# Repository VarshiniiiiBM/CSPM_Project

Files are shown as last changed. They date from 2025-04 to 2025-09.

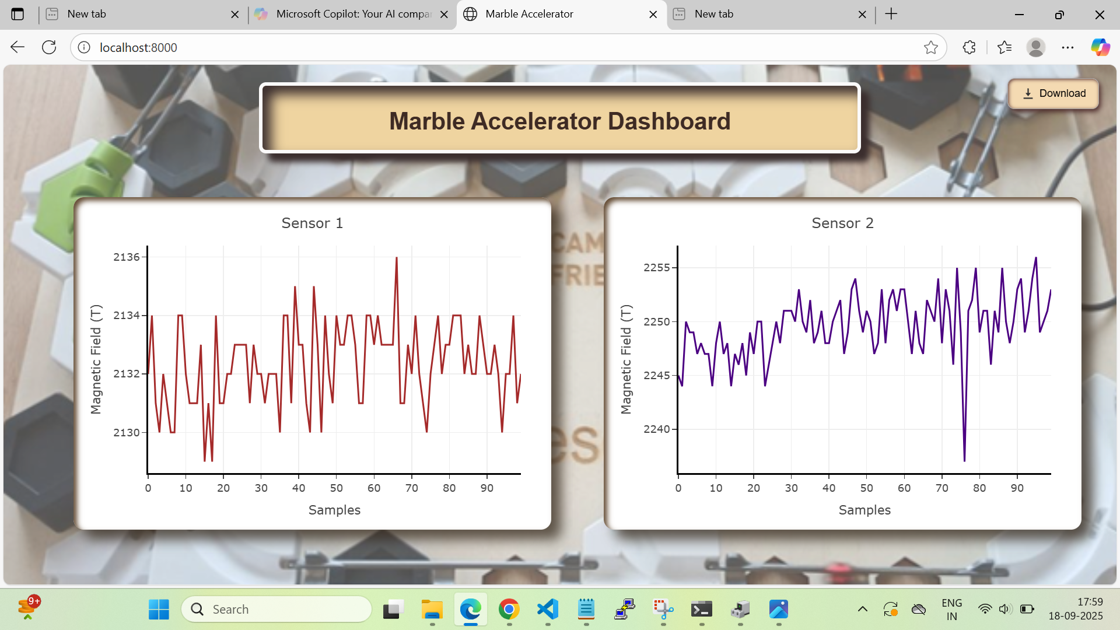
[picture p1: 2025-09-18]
Data_visualization/Fastapi_webserver/Result_img/img_3.png

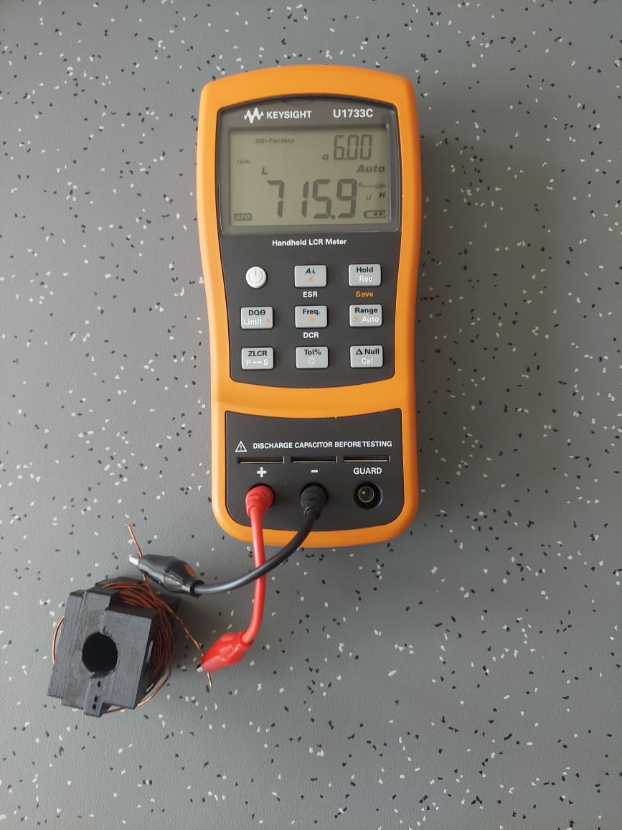
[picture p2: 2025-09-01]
Induction measurement/Coil 2 Inductance.jpeg

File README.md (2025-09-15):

# CSPM_Project
Marble Accelerator

## Team 

Members:

- Varshini Barallu Manjunath
- Rohith Joy
- Murtuza Udaipurvala
- Abdul Manaf 
- Anisha Bhanderi
- Smit Patel Kumar
- Fabian Mink (Supervisor)

## Links

Hessenbox: https:https://next.hessenbox.de/index.php/s/KFFSPPiGzwdTdbN

## Rules for writing equations, physical units and quantities

When formulating expressions, the internationally recognized rules of the SI system must be strictly adhered to. This applies to both presentation slides and reports. Failure to comply with these rules will result in a significant reduction in the grade for the formal criteria of the project work.

The SI-Brochure provides a good overview:

https://www.bipm.org/en/publications/si-brochure

A checklist can be found at the beginning of this document, pages v - vi:

https://physics.nist.gov/cuu/pdf/sp811.pdf

## Components

List of items borrowed from Fabian to be returned at the end of the project:

- Gravitrax Components (Box, Baseplate, 2x Curves, curved tunnel, 2x rails, sample coil designs)
- BTS7960 H-Bridge Board
- KY-035 Hall Sensors
- 2x Board STM32L476 Nucleo, 1x USB Cable
- Capacitor 22mF, 50V and Capacitor bank 20x1.5mF, 25V (2025-06-12)
- Lab Power Supply PeakTech 6226 (2025-07-01)
- Oscilloscope TDS 1012 + 2 Probes + USB CF Card Reader + Transport Bag (2025-09-15)

The project grades will only be entered into the examination system when all parts have been returned in good condition!

## Presentation And Report 
- Report Submission Date : 19th Semptember
- Presentation Submission Date : 21st Semptember
- Presentation Data : 23rd Semptember 
- Presentation Format: Total 20 min, including 5 mins for project video.

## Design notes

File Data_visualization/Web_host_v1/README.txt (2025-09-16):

# STM32 Real-Time Data Visualization
 
This Python script enables real-time data visualization of sensor data from an STM32 through serial communication. The data can be visualized both on a desktop application (PyQt6) and on a web interface (Plotly.js), accessible remotely through FastAPI, WebSockets, and ngrok. A QR code is generated at runtime, allowing instant access to the live charts on mobile devices.

## Features

* **Real-time Data Streaming**: JSON chunks sent every 10 ms, each containing 100 samples of D1–D3.
* **Derived Parameter (D4)**:Is computed from (D1)[asumed as Kinetic Energy].

* **Desktop Visualization**:

  * PyQt6 window opens automatically on script execution.
  * Charts for D1, D2, D3, and D4 with automatic Y-axis scaling.
  *An update from  Matplotlib has been applied for smooth rendering and lag-free visualization.

* **Web Visualization**:

  * FastAPI + WebSockets for real-time data broadcast.
  * Ngrok tunneling removes dependency on the same local network.
  * Multiple devices can be connected simultaneously by scanning the QR code generated.
  * QR code generation for quick mobile access.
  * Charts can be downloaded directly on mobile or PC.
  * Accessible on PC locally where script is run, on browser at `https://<PC-IP>:8000`.

* **Reset Functionality**: Data clears automatically when STM32 reset button is pressed.

---

## Data Format

Example JSON chunk received from STM32:

```json
{
  "D1": [1.61, 1.61, 1.61, ...],
  "D2": [84639, 84640, 84641, ...],
  "D3": [-200, 200, -200, ...]
}
```

---

## Workflow

1. STM32 sends JSON chunks every 10 ms.
2. Python script processes data
3. Data is plotted in PyQt6 window(desktop).
4. Data is also broadcast to web clients via FastAPI + WebSockets.
5. Ngrok provides external URL + QR code for mobile visualization.
6. Charts can be viewed, downloaded, and reset from either interface.

---

## Accessing the Web UI

* On **Mobile**: Scan the QR code generated in the terminal.
* On **PC**: Open `https://<PC-IP>:8000` in browser.
* Multiple devices can connect at the same time.

---

## Requirements

* Python 3.10+
* PyQt6
* Plotly.js
* FastAPI
* WebSockets
* Ngrok

+++ An index.html file for web page UI has also been created and added separately, and should be in the same folder as the main.py while running the script
---

## Summary

This system ensures real-time, smooth, and lag-free visualization of STM32 sensor data across both desktop (PyQt6) and web (Plotly.js) platforms. The ngrok integration enables remote access without network restrictions, while the QR code feature makes it easy to open live charts on mobile devices.

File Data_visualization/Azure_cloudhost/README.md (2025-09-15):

#  STM32 → Azure Web App → Browser (Real-time Data Streaming)

This script enables **real-time data streaming** from an STM32 microcontroller to a mobile/web browser using **FastAPI** hosted on an **Azure Web App**.  
It is designed for remote access to sensor data in a secure and reliable manner.

## Significance and Idea Behind Implementation

The script showcases how STM32 sensor data can be accessed remotely via the cloud instead of being limited to a local PC. By using Azure Web App and WebSockets, it demonstrates a  IoT-style approach, enabling secure real-time data access from any device. This enhances learning outcomes by combining hardware, networking, and cloud technologies into a practical end-to-end system.

---

## Project Structure

### 1. **Azure Web App (Cloud-side)**
- **File:** `main.py`  
- **Description:**  
  - Implements a FastAPI backend deployed on Azure Web App.  
  - Provides:
    - `/` → Serves the `index.html` dashboard.  
    - `/ws` → WebSocket endpoint for pushing live data to clients.  
    - `/ingest` → API endpoint for receiving sensor data from STM32.  

- **File:** `index.html`  
  - Frontend web page that connects to the `/ws` WebSocket and displays real-time charts of the streamed data.

### 2. **Local PC (Edge-side)**
- **File:** `serial_reader_pc.py.py`
- **Description:**  
  - Connects to STM32 board via serial (USB COM port).  
  - Reads sensor data from STM32 in JSON format.  
  - Processes and augments data (`D1`, `D2`, `D3`)  
  - Sends the data to Azure Web App (`/ingest`) via HTTPS POST.  

---

## Data Flow

1. STM32 → Serial (JSON data).  
2. Local PC script (`serial_reader_pc.py.py`) → Parses JSON and sends securely over HTTPS to Azure.  
3. Azure Web App (`main.py`) → Receives data and broadcasts via WebSocket.  
4. Browser (`index.html`) → Connects to WebSocket and shows live data charts.  

---

## Usage

1. Deploy `main.py` + `index.html` + `requirements.txt` to Azure Web App.  
2. Run `serial_reader_pc.py` on the local PC connected to STM32.  
3. Open your Azure Web App URL in a browser (PC or mobile).  
4. View live sensor charts streamed securely via Azure.

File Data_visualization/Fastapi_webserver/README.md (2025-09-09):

# FastAPI WebSocket Serial Data Broadcaster

This script opens a FastAPI server that:
- Reads JSON-formatted data from a serial port
- Broadcasts the data in real time to all connected WebSocket clients.
- Serves HTML file named "frontend.html" to view raw incoming data in the browser.

## Features
- Reads serial data from a configurable COM port and baud rate.
- Parses newline-separated JSON objects.
- Broadcasts parsed data to all WebSocket clients simultaneously.
- Uses Python’s "logging' module for structured logs instead of "print".
- Adjustable "debuglevel" variable for fine-grained debugging.

##Logger and Debug Option
-This script uses Python’s logging module instead of print to handle all output.
Logs are timestamped and categorized by severity (DEBUG, INFO, WARNING, ERROR).
This makes it easier to filter messages.

## Debug levels
Controlled by the debuglevel variable at the top of the script:

0 → Only ERROR messages (minimal logging)

1 → WARNING + ERROR

2 → INFO + above

3 → DEBUG + above (most verbose, includes raw details)

This allows to adjust verbosity without editing multiple lines of code.

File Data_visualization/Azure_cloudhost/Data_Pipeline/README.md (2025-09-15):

For deployment, after updating the code, the files (main.py, index.html, and requirements.txt) were placed into a single folder. The VS Code Azure Web App extension was then used for easy deployment to the Azure Web App named serial-ws-backend.

In the Azure Web App Settings → Configuration, the startup command was set to:
python -m uvicorn main:app --host 0.0.0.0 --port 8000

Debugging was performed using the Log Stream output messages. The data pipeline was first tested by sending sample data through this channel, and then switched back to live data, which worked successfully. The UI was also improved with different colors and additional padding for the charts.

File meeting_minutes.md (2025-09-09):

# Meeting 2025-09-04

Location: A4.U1.21 Time: 13:00

Minutes Made by Anisha

- Participants:
- Abdul Manaf Mansoor
- Anisha Bhanderi
- Murtuza Udaipurvala

Suggestions by professor:

* Timestamp should also be sent along with the data.
* Add meaningful comments in the code for readability and easy understanding.
* Remove the code, which has been used for UI freezing scenario.
* Rename files with descriptive names, so it can be known that what is there in the file.
* Separate python programs for both, Webserver and QT charts. 
* Web version should be preferred for further changes.
* Add debug level and make debug info output dependent on assigned debug level.
* Remove all warnings from STM32 code and upload complete code on Git.

# Meeting 2025-07-22

Location: Lab Time: 12:30 am

Minutes Made by Abdul Manaf Mansoor.

- Participants:
- Varshini Barallu Manjunath
- Rohith Joy
- Murtuza Udaipurvala
- Abdul Manaf Mansoor
- Anisha Bhanderi
- Smit Patel
- Prof. Mink

Discussed Topics

1. Final Coil Model(Rohit) : Two coils will be used in the design one on the top and one on the bottom—mounted. The model will be 3D printed and ready by tomorrow. Smith and Murtuza will handle the winding process.
* Feedback from Professor : Focus on completing the project. Get the first prototype printed and ready for testing. Might need more changes.

2. Capacitor Calculation(Smith): Discussed energy calculation using capacitor formula (1/2)*C*V^2. Discussion of mechanical energy conversion. 
* Discussion with professor : Energy efficiency is below 10% based on observations from the previous project. Work done and energy loss were calculated for a 20A current coil. Picture Attached in Hessenbox.
   This calculation should be included in the report.

3. Discussion of Work Plan (Murtuza) : Discussed work plan packages for everyone.
              1) Extended Existing Design with new hardware:
                  a) Motor Controller
                  b) STM32 Board
                  c) Python Dashboard
                  d) Matlab Simulation
               2) New Coil Model:
                  a) 3D printing new model
                  b) Winding New model
                  c) Magnetic sensor

4. Python Dashboard (Manaf) : Dashboard updated with time in Millisecond presented.
*   Feedback from Professor: The dashboard still has dummy data in seconds. The dashboard display a burst of data and then stop. The dashboard is cleared and new data is plotted when it arrives. Next demostration should
   get data from microcontroller. This could be achieved by having a button on microcontroller that sends burst of data when it is pressed. This data is received on serial and then plotted.

General : During the leave period, meetings should be held once a week, and the minutes should be updated. Lab access requires safety and security instructions to be given first by Mohammed Shaami. Everyone’s vacation
plans should be discussed.

# Meeting 2025-07-01

Location: A3.2.08 Time: 10:00 am

Minutes Made by Abdul Manaf Mansoor.

- Participants:
- Varshini Barallu Manjunath
- Rohith Joy
- Murtuza Udaipurvala
- Abdul Manaf Mansoor
- Anisha Bhanderi
- Smit Patel
- Prof. Mink

Discussed Topics

1. Coil Inductance Calculation
   
* Discussed methods to verify the accuracy of inductance measurements:
* Use of FEMM was discussed.
* Possibility of using an LCR meter was also discussed.
* Professor inquired about expected accuracy of the measurements; suggested that an accuracy of ±20% is acceptable.
* Professor emphasized that the marble's permeability will have a significant influence on the inductance (increase of inductance by 20...50%, maybe even more). So it does not make sense to calculate an "accurate" value for inductance without considering the marble. Consequence: A rough estimate of the inductance is sufficient. Basic inductance estimation formulas (e.g. https://en.wikipedia.org/wiki/Solenoid or https://de.wikipedia.org/wiki/Zylinderspule ) can be used.

2. 3D Printing and Accelerator Design

* Professor reiterated the goal: to develop an efficient accelerator, not just focus on the tube design. Tasks that must be completed to pass the project are listed in the pdf "Marble Accelerator Project" (p.3 "Tasks") which was presented in the Kickoff-Meeting and uploaded to Moodle at the beginning of the project in april.
* Advised to begin prototyping the accelerator.
* The current 3D modular design presented is having 75 to 85% success rate.

In the remodeling discussion:

* Emphasized the need to consider space for the marble to come to rest.
* Discussed forces acting on a marble at rest.
* Demonstrated a basic graph and force equation to estimate the minimum current needed to move the marble from rest.

3. Data Visualization
   
* Professor provided the following suggestions:
* Adjust x-axis scaling to reflect realistic project values.
* Replace current pulse animation of capacitor with a capacitor energy graph.
* Position graph should be in centimeters (cm), not meters.
* Time axis should be in milliseconds (ms).
* Graph should reset for each new data chunk to avoid overcrowding.
* Professor agreed on the use of wireless communication for data transfer but emphasized that the accelerator development must be prioritized.

4. Presentation Guidelines

* All missing PowerPoint presentations should be uploaded to Hessenbox.
* Reviewed checklist on GitHub regarding SI unit standards:
* Emphasized strict adherence in all presentations and reports.
  
Professor demonstrated:

* How to insert formulas in PowerPoint and the available formatting options.

Clarified usage of unit notations:

* Do not use parentheses (), square brackets [], or curly brackets {} for SI units, as it means multiplication, the unit of.., and the numerical value respectively.
*  Use a forward slash (/) instead.
* In mail, it was clarified by the professor regarding the usage of brackets.
* Detailed explanation on bracket usage is available in Chapter 7.1 / Page 15 of the PDF (link uploaded to GitHub).

5. Next Steps & Meeting Schedule

Due to upcoming exams:

* Next meeting to be postponed.
* Professor will be on holiday from July 25 for 3 weeks.
* Last available date for meeting before vacation: July 22.
* Target: Have the accelerator and prototype ready by then.
* Suggested to contact Shami for equipment requirements. Remark (Fabian): Shami has been informed that he can supply copper wire of a certain length /cross-section previously calculated by you (e.g. "20m of wire with 0.75mm diameter) for building accelerators. He will not issue any other components without prior consultation with me. Last opportunity to discuss this before my vacation: July 23rd.

# Meeting 2025-06-17

Location: A3.2.08 Time: 11:30 am

Minutes Made by Smit

- Participants:
- Varshini Barallu Manjunath
- Rohith Joy
- Murtuza Udaipurvala
- Abdul Manaf Mansoor
- Anisha Bhanderi
- Smit Patel
- Professor Mink

- Coil wire diameter calculation were presented by murtaza.
  Professor said calculation seems correct but also calculate inductance and time constant for wire diameter.

  Feedback by professor on presentation and slides.

  Introductory slides and presentation

- First part of presentation and slides were good.
- Phase slides were good but have been improved by adding key points.
- In simulation formula symbols were missing. (eg. for turns write N.)
- Not proper explaination for the data for eg. Coil inner radius and coil length.
  Explain values in image with arrow mark so everybody can understand.
- How to calculate force on marble explain this part in slide.
- In matlab simulation slide explain what final values are we getting and add explaination for velocity
  and position block with marking.
 - For coil wire optimization it coulbe better if photo of coil and marble accleration were provided
   at the beginning.
 - Title of STM32 should not be reprogramming.
 - For data visualization pictures could be better.
 - Coil carrier design will not work because of coil mount. Marble will not comes out from coil.

   Overall feedback by prefessor on presentation.

- Explain content of slides properly and give enough time to read slides.
- For 15 mins of presentation there should be 12 slides.
- If all are agree then we can do small presentation before final one to get feedback from professor.

  Next week's Agenda and meeting minutes will be done by Abdul Manaf. He will also give a short overview of the agenda at the beginning (2 to 3min)

# Intermediate meeting  2025-06-15

Location: Steinkaute , Friedberg Time: 1 pm

Minutes made by Smit

- Participants:
- Varshini Barallu Manjunath
- Rohith Joy
- Murtuza Udaipurvala
- Abdul Manaf Mansoor
- Anisha Bhanderi
- Smit Patel

Agenda :
About mid term presentation/ presentation slides and dividing tasks/discussion about overview of project 
and future work.

Phase-1
In this phase we discuss about tasks which was compulsory for all students.
-3D - Modeling of coil carrier
-FEMM Magnetic simulation and calculation based on that.

Phase-2

Brainstorming

In this phase we had discussion about what new things we are doing in project and what results we had achieved so far.
- Hall effect sensor design by Varshini and Rohith.
- Matlab simulation for overall system by Murtaza.
- Data visualization using Python matplot liberary by Anisha and Manaf.
- Coil wire optimization and calculation for it by Smit.
- Redesign of Coil carrier by Rohith and Varshini.
- STM32 Reprogramming by Murtaza.

  Phase -3

  Future Work
  
  In this phase we had discussion about task which are still pending and ideas needed for it.
  - Coil carrier and hall effect sensor designs are still not confirmed.
  - Power electronics for overll circuit. there is still some calculation we have to do for
    capacitance.

# Meeting 2025-06-03

Location: A3.2.08 Time: 10:00 am

Minutes Made by Anisha

- Participants:
- Varshini Barallu Manjunath
- Rohith Joy
- Murtuza Udaipurvala
- Abdul Manaf Mansoor
- Anisha Bhanderi
- Smit Patel
- Professor Mink
- Professor Klein
  
Anisha Bhanderi
* Overview of the Agenda explained

Discussed Topics

Anisha and Manaf 

* Data visualization of CSV, before using JSON format
* Made changes in the Python code according to the JSON data structure
* Explained the code used for plotting
* Visualized the data on Matplotlib and showed the result in graphs 

Feedback by Professor:

* Change the range of the 2nd graph, no need to use delta
* Change the JSON structure to reduce the number of bytes used
* Do not use unarranged putty values in future presentations

Smit Patel

* Selected coil wire of diameter 0.2 mm
* Reasons behind choosing thin wire: More number of turns, higher resistance, Stronger magnetic field
* Inductance is calculated by using a lua script
* Explained the calculation for resistance after changing the number of turns with a thinner wire.

Feedback by Professor:

* Question was asked: Why do you use thinner wire if you are not increasing the number of turns as expected?
* Higher resistance is not good. If resistance is higher, then we have to generate more energy, and for storing energy, capacitors with higher capacitance will be needed.
* Feedback for slides: Use units for each value. (website will be provided by Prof)
* For slides, containing more formulas: Write in more arranged way, it should not be concentrated at one place. Use a subscript when needed

Murtuza

* Saved sample data in a buffer and sent it on the UART in JSON format.
* Scheduling Systick for every 1 ms interrupt.
* Configuring the Timer to generate data every 0.1 ms interrupt. Timer is running at 10 KHz.
* Further tasks: Detecting Marble entry with Hall Effect sensor, Calculating Marble velocity. 

Feedback by professor:

*	For JSON data structure: Use array of values for all three data. By doing so, less number of bytes will be used and it will be easy to extract data for the other subteam.
*	While using readp and writep, a race condition can create a problem, which can lead to missing data or changing and getting the wrong data.
*	Same with send_data_flag as well

Rohit and Varshini

* 3D model for testing and tuning the hall effect sensor: to detect the position and calculate the speed
* For sensor placement: measured the sensor and keep a bit more space for ease
* Three differently inclined (10,20,30 degrees) models to check the change in speed
* Coil carrier to redirect marble right-angle upwards
* Two sensors placement: one on the center of coil winding and other one on the top
* Suggestion of using two windings: One where the marble enters and other one from where the marble goes out
* Concerns:

    o	Whether we can throw a marble to the top
  
    o	If we increase speed, it can damage the edges of the coil carrier at log run
  
    o	Which one will be better: right-angle coil carrier or inclined at some angle

Feedback by Prof Klein:

*	Got a general overview of the work, understood sketches
*	Question related to calculation: What will be the force to send the marble on top? What will be the speed of the marble?

Feedback by Prof Mink:

* Do some calculations like height, force, energy, speed of a marble, etc. It should be a priority to understand physical functionality
* Question: Why is there a square shape design (the same as winding design) on the top?
  Answered by Rohit: If one coil winding is not able to generate energy, then it will be easy to design a second winding design
* There should be one more sensor, to detect when the marble enters 

Professors' Overall instruction:

* Think of different coil carrier design
* Include name and slide number on slides from the next meeting
* Font size should be the same for all (16 px)
* For code, do not use black background. Try to use white to make it easily visible
* If the code is important and you want to explain it, then only include it in slides
* Before the presentation, merge all slides and upload to Hessenbox

Discussion about different designs of coil carrier:
* In vertical structure, there will be space where marble can rest. Therefore, there will not be a requirement to use a sensor at the entrance, to detect when marble enters
* The same idea can be implemented for inclined structures
* Compared to inclined structures, vertical structures need less force, because friction will be less in vertical structures

Feedback and suggestions by Prof Klein:

* It looks like team members are not connected; all are working just for their own part of the project.
* Start working as a team, there should be an idea of who is working on which part of the project
* Write a To-Do list and interface in every meeting
* What can be done to go to performing stage from storming phase?
* Use strategy of three flags

    o	Green flag – work has been done in time
  
    o	Yellow flag – work has not been done in time
  
    o	Red flag – work has not been started yet
*	Be responsible for your part of the project, while keeping a general idea about the whole project
*	Discuss in a team, each member should know some points: Definition of project, work packages, milestones, and what a common target is.

Next week's Agenda and meeting minutes will be done by Smit Patel. He will also give a short overview of the agenda at the beginning (2 to 3min)

# Meeting 2025-05-27

Location: A3.2.08
 Time: 10:00 am

Minutes Made by Varshini
Small corrections / clarifications by Fabian (2025-05-30)

- Participants:
- Varshini Barallu Manjunath
- Rohith Joy
- Murtuza Udaipurvala
- Abdul Manaf 
- Anisha
- Smit Patel Kumar
- Abhyshek Rajmohan
- Professor Mink

10.00 - 10.10 - Varshini
* Overview of the Agenda explained

10.10-10.25- Rohith and Varshini

* Slicing and 3D printing coil carrier, converting stl files back into CAD files

Feedback by Professor:
* Need to work on redesigning the coil carrier

10.25 - 10.42- Murtuza

* Explained code of uart to transmit test values on serial.
* Further task, Sample data at a high rate ( 10khz and send it on uart in bursts, every 5 seconds.)

Feedback by Professor:

* Use some JSON Structure (https://www.json.org) or define 1 start / stop character or string (e.g. "START" / "STOP") that will never happen in data (should be discussed with the team)
* Sending data every 50 ms is not useful, as sampling rate will be 10kHz or more
* In transmission of data there should be more delay
* Put the data sheets in the hessen box 
* Change the baud rate if it is not fast enough

10.45-10.52 - Manaf and Anisha

* Used Putty application 
* Code is in development state 
* Once the data structure is given changes in the code will be done 

Feedback by Professor:

* More work to be done on the code
* Update the code in the Github 

10.52-11.02 - Smit

* Went through the Magneto Static Tutotrial 
* Solution  is uploaded in the GitHub
* Once coil carrier is confirmed design will be created in FEMM
* Measurement of the wire, Magnetic force needed to push the marbel will be calculated
* First simulation is done and then its implemented

Feedback by Professor:

* Simulation should be uploaded 
* Take the existing one and optimize it 
* Think of different simulating design (For example: Diagonal, 45 degrees) and how to 3D model and simulate
* Calculate Resistance and Inductance to make sure it will work with 24V
* How to calculate Inductance?
* Maybe more windings?? higher for the marbel but same current??(needs to be decided and if agreed calculated)
* For the question asked by smit- How to calculate magnetic force? 
  - its done in the test 
  - its there in the lua code
  - it depends on how high you want to shoot the marbel
* Suggestion by professor - wire diameter 0.5mm ... 0.75mm seems to be optimum according to experiences made with previous designs; but also other diameters might work

11.04-11.10- Professors Overall Feedback to everybody

* Include more slides from next meeting 
* In the next weeks meeting along with Prof Klein everybody must present for 5 mins (min 4 - max 6)
* Focus more on the results of what we have done in the project already and not what you are planning to do; there can be a small outlook for future work (1 min for each student)
* See the coil of the other group.

1.Next weeks Agenda and meeting minutes will be done by Anisha. Please prepare everything (switch on the projector etc...) so that we can directly start 10:00 without further delay. Anisha will also give a short overview of the agenda at the beginning (2..3min)

2.Smit will collect the wire from professor at 9.00 am in the lab

11.10-11.30 - Abhyshek

* Questions asked about concept of coil gun, servo motors, controlling the angle of the coil gun, is it feasible to go with the coil?
* Sugesstion by Professor-

1.Potentional Engergy must be calculated

2.Number of Turns and Voltage is calculated by FEMM software

3.Luna script can be found in the GitHub

# Meeting 2025-05-08
Meeting time and location: 2025-05-08, 09:00; 

minutes kept by:  >>Rohith Joy<<

Participants:
- Rohith
- Murtaza
- Anisha
- Prof. Mink

Diskussed Topics:
- Generate a hessenbox link
- ppt on Project parts done by each member.
- Grundgesetz
- materials used to 3D print
- Purchasing hall-effect sensors
- FEMM test on next week
- Output measurement data via serial interface; plotting of values
- Generating a code with dummy values on STM board for plotting in MATLAB

Tasks todo until the next meeting:
- Abdul Manaf: prepare for FEMM test 
- Anisha: prepare for FEMM test
- Fabian: Prepare test on FEMM magnetic field simulation; provide sketches for CAD designs; Dynamic simulation
- Murtuza:prepare for FEMM test; Purchase quotation for hall-efect sensors 
- Rohith:prepare for FEMM test
- Smit:prepare for FEMM test
- Varshini:prepare for FEMM test

Next meeting: 14th May at 2:00 PM

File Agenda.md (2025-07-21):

# Agenda meeting 2025-07-21

Meeting Time: 21.07.2025, 12:30 pm;
Location: Lab (Room No)

Participants:
- Varshini Barallu Manjunath
- Murtuza Udaipurvala
- Rohith Joy
- Manaf Mansoor
- Smit Patel
- Prof. Mink

Tasks Done This Week:

*Rohith and Varshini:  Coil Redesign Model

On the day of the meeting: 

*12.30 - 1.00 - Finallizing the Coil Model Design and Discussion of future steps

*1.00 - 1.15 - Indutance Mesurement and Winding Machine Demonstration

*1.15 - 1.30 - Discussion and Question to professor. 

# Agenda meeting 2025-07-01

Meeting Time: 01.07.2025, 10 am;
Location: A3.2.08

Participants:
- Varshini Barallu Manjunath
- Murtuza Udaipurvala
- Rohith Joy
- Anisha Bhanderi
- Manaf Mansoor
- Smit Patel
- Prof. Mink

Tasks Done This Week:

*Rohith and Varshini:  Coil Redesign

*Manaf and Anisha: Development of wireless communication between the STM board and PC for data transfer, with potential chart integration in the dashboard.

*Smit: Coil wire diameter calculation.

*Murtuza:  Inductance calculation and stm32 code for sending json data in array format.

On the day of the meeting: 

*10.00 - 10.35 - Everybody will explain about their tasks done in the last week.

*10.35 - 10.50 - Any doubts or suggestions.

*10.50 - 11.00 – To Do list (Discussion within the group) 

# Agenda meeting 2025-06-03

Meeting Time: 03.06.2025, 10 am;
Location: A3.2.08

Participants:
- Varshini Barallu Manjunath
- Murtuza Udaipurvala
- Rohith Joy
- Anisha Bhanderi
- Manaf Mansoor
- Smit Patel
- Prof. Mink
- Prof. Klein

Tasks Done This Week:

*Rohith and Varshini: Re-modelling of the coil carrier (3D printing)

*Manaf and Anisha: Visualisation of sample data using matplotlib, made changes in code to parse JSON file

*Smit: Selection of coil wire diameter, Calculating inductance using a Lua script, and calculating resistance to work with 24V

*Murtuza: Worked on the code for sending data in json format, implemented systick and simple timer scheduling of idle processes and generating data.

On the day of the meeting: 

*10.00 - 10.30 - Everybody will explain about their tasks done in the last week.

*10.30 - 10.40 - Any doubts or suggestions.

*10.40 - 11.00 - Feedback from Prof. Klein regarding the process and organization of the project meetings, suggestions for improvement.

*11.00 - 11.10 - Agreemens on how to use the GIT repository incl. Agenda and Meeting Minutes (Fabian)

# Agenda for meeting 27.05.2025

Meeting Time :27.05.2025, 10 am
Location:A3.2.08

Participants:
Varshini
Murtuza
Rohith
Anisha
Manaf
Smit
Abhyshek
Prof. Mink

Tasks Done in this week:

*Rohith and Varshini: 3D printing the vertical and horizontal designs of the coil carrier

*Manaf and Anisha: Data visualisation using matplotlib on sample data

*Smit: working on coil designing and simulation for coil designing in FEMM

*Murtuza: Interfacing sensor hall effect sensor with stm32board

On the day of meeting: 

*10.00 - 10.30 - Everybody will explain about their tasks done in the last week.

*10.30 - 10.40 - Discussion with professor

*10.40 - 10.45 - Professor will provide idea about the next meeting

*10.45 - 11.00 - Discussion with Abhyshek about the doubts

*Abhyshek -  would like to know the specifics of the electromagnetic coil launcher. What kind of circuit was used for vertical launch, mosfets for timing and whether a capacitor would be necessary. Also the feasibility of launching about 1 metre.

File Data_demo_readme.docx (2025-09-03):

Data:

Comma separated values on serial port. Baud rate - 115200

Format:

Data_1,Data_2,Data_3\n

Data_1 is a float value, Data_2 and Data_3 are integer values.

Verification

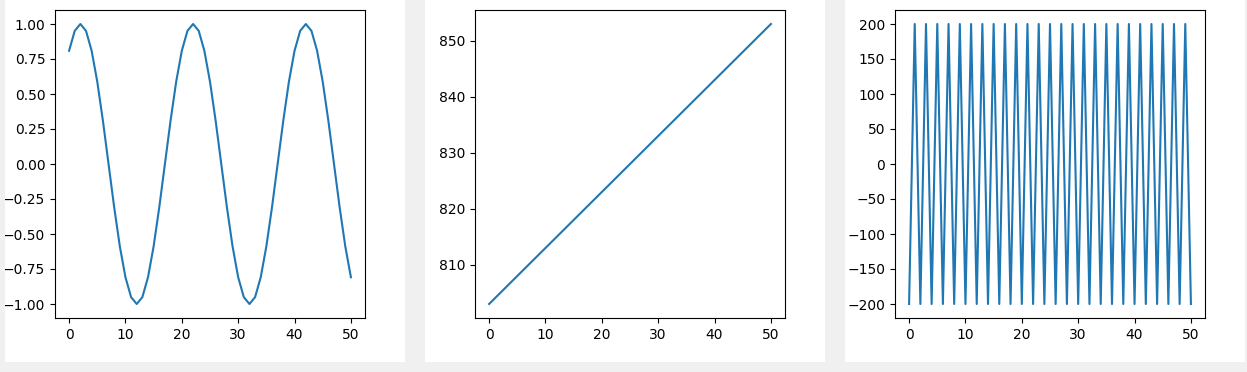
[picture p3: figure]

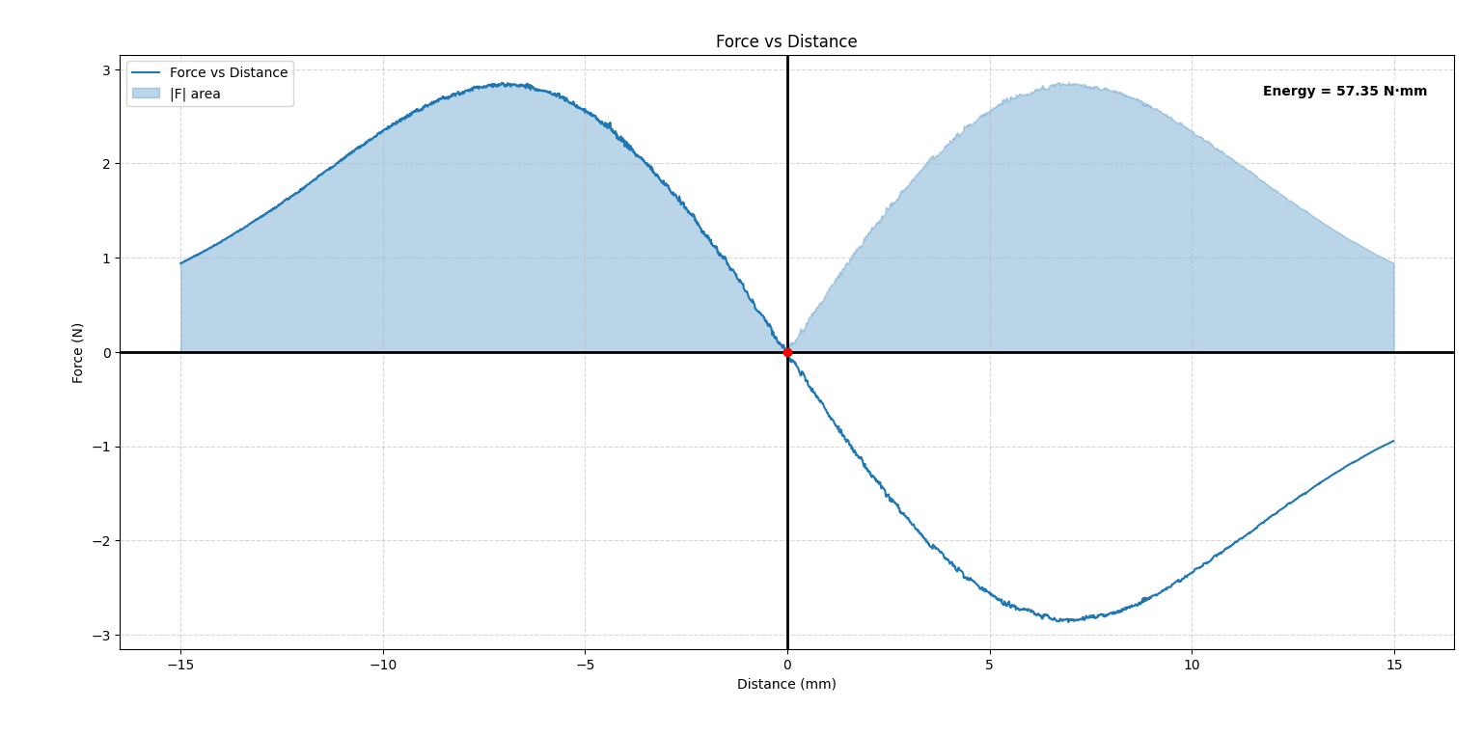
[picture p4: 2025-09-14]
Mechanical energy calculation/Figure_1.png

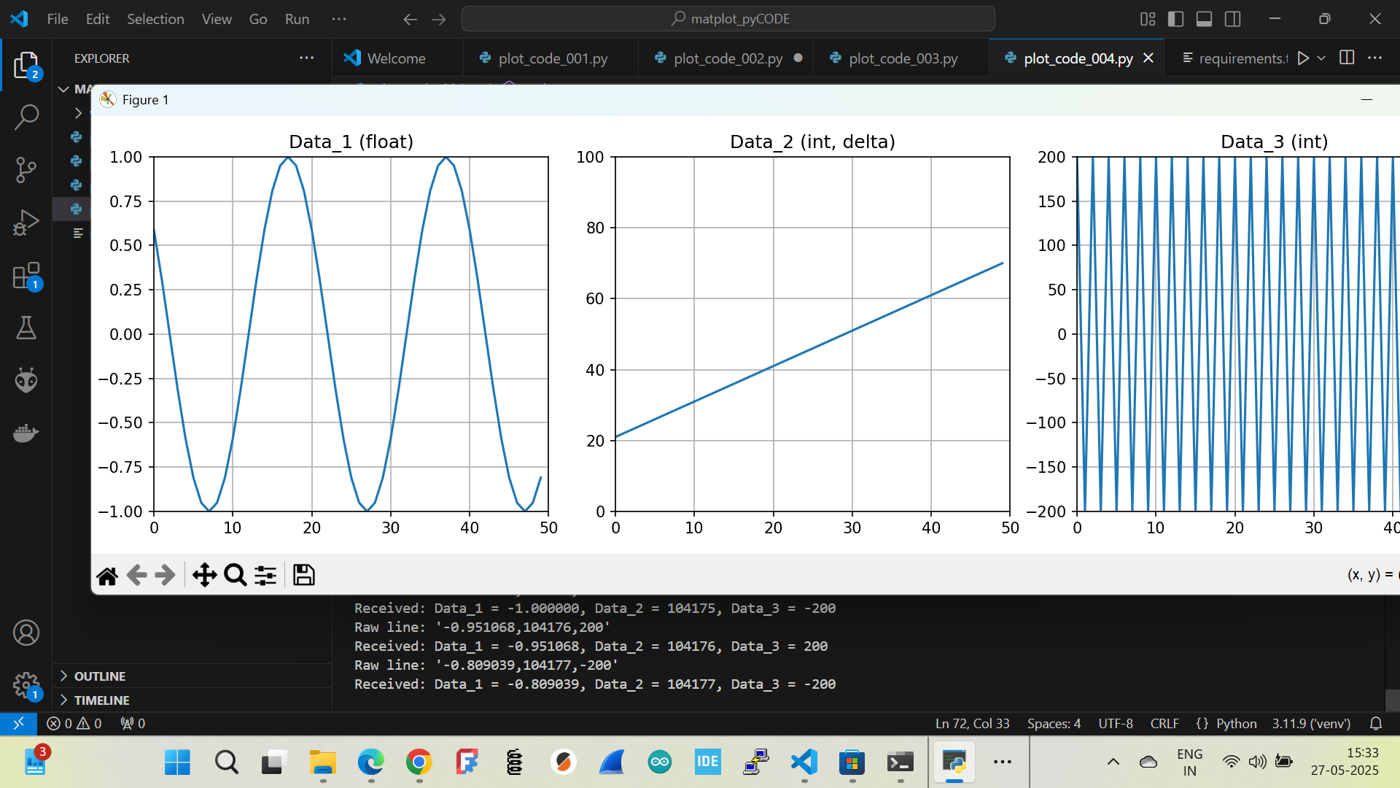
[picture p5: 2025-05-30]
Data_visualization/sample_plots.png

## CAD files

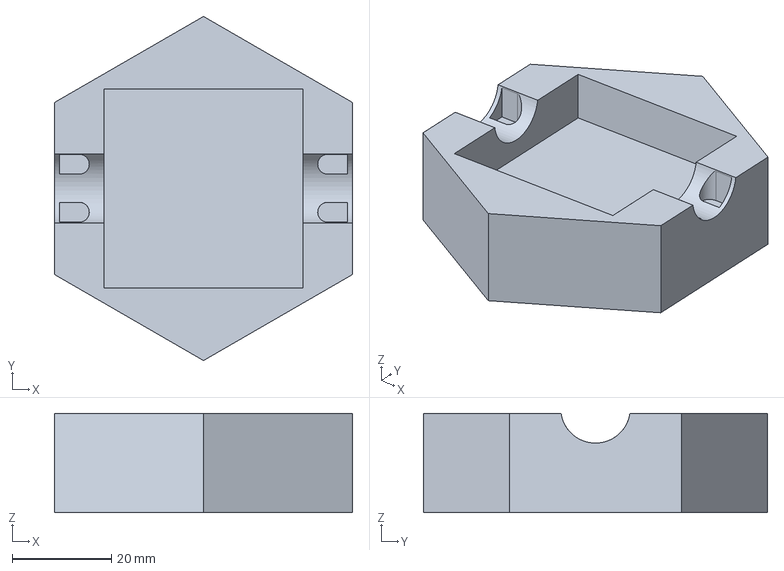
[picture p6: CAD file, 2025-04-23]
CAD/CAD Design.FCStd
60.0 x 69.3 x 20.0 mm

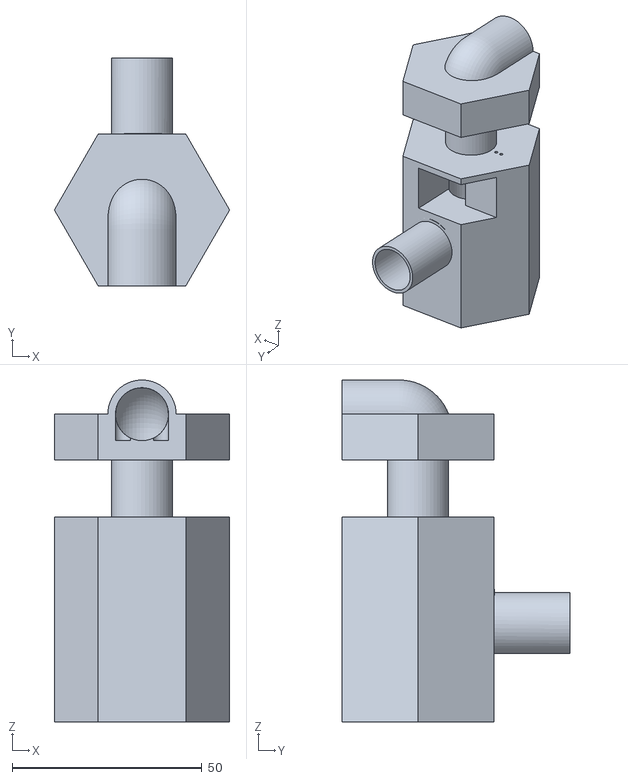
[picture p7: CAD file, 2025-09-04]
CAD/Coil_Redesign_Version3/Coil_Vertical V3.stl
46.2 x 60.0 x 90.1

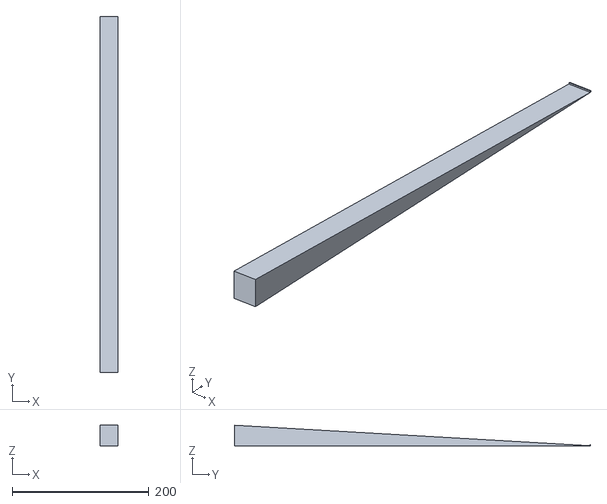
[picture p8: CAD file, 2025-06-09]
CAD/Halleffect_Sensor_Tuning/30degree_incline.stl
26.0 x 520.1 x 30.0

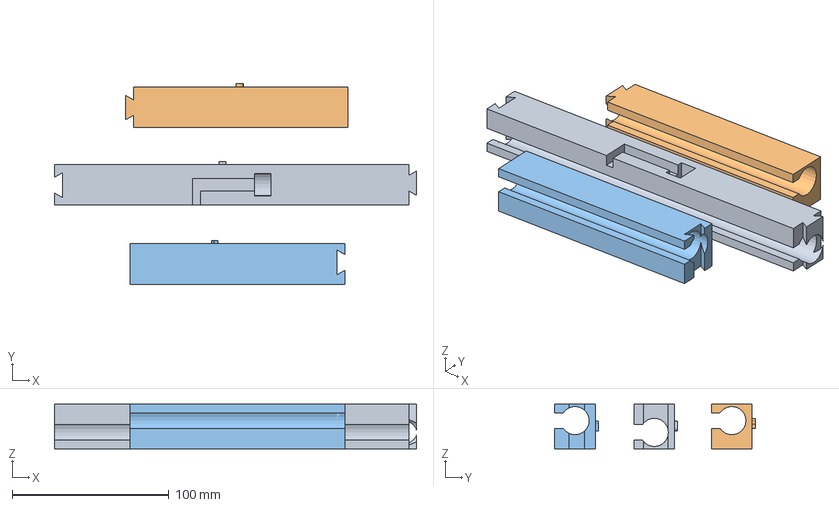
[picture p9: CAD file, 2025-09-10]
CAD/Halleffect_Sensor_Tuning/V4/Hall_effect_sensor_testing_V3 v3.2.3mf
230.9 x 128.0 x 28.5 mm
Hall_effect_sensor_testing_V3 v3.2.stl_B_A
Hall_effect_sensor_testing_V3 v3.2.stl_A
Hall_effect_sensor_testing_V3 v3.2.stl_B_B

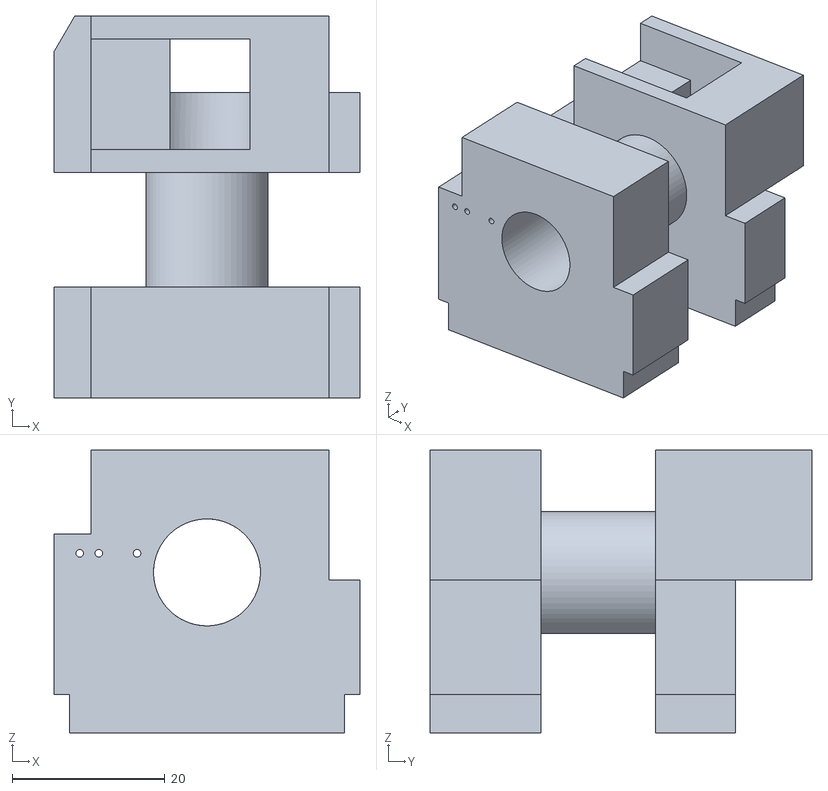
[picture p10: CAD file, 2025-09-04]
CAD/Coil_Redesign_Version3/Coil horizontal V3.stl
40.0 x 50.0 x 37.0

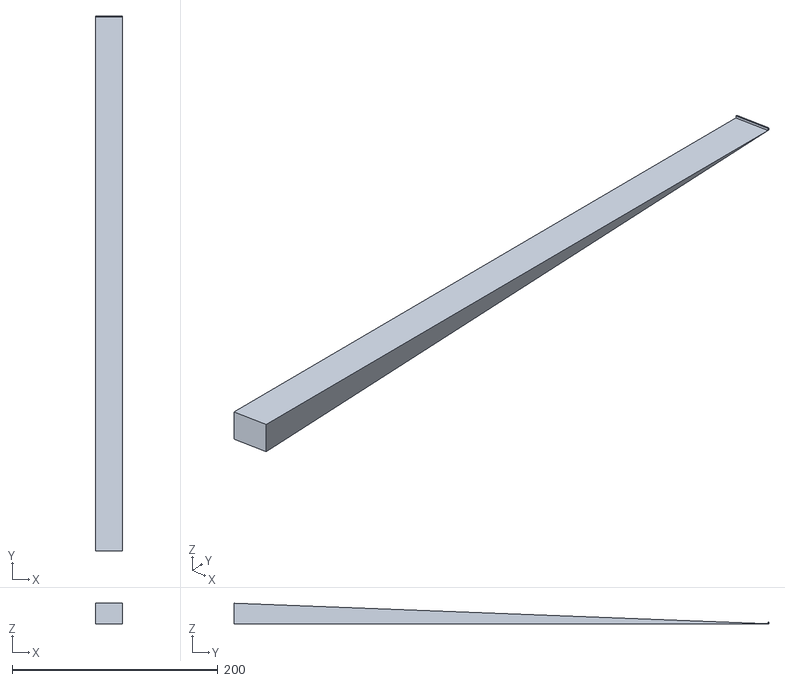
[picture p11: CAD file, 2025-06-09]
CAD/Halleffect_Sensor_Tuning/20degree_incline.stl
26.0 x 520.1 x 20.0

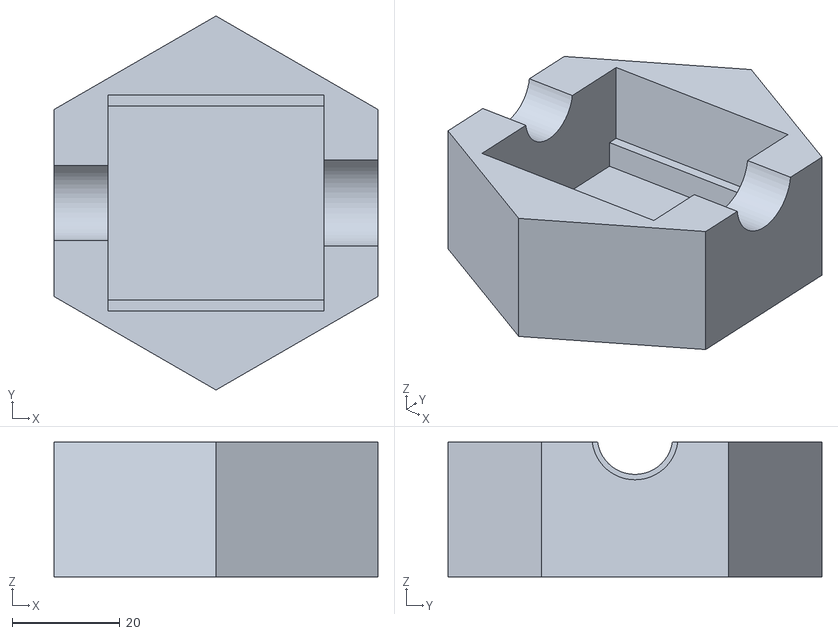
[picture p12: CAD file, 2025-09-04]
CAD/Coil_Redesign_Version3/Coil base V3.stl
60.0 x 69.3 x 25.0

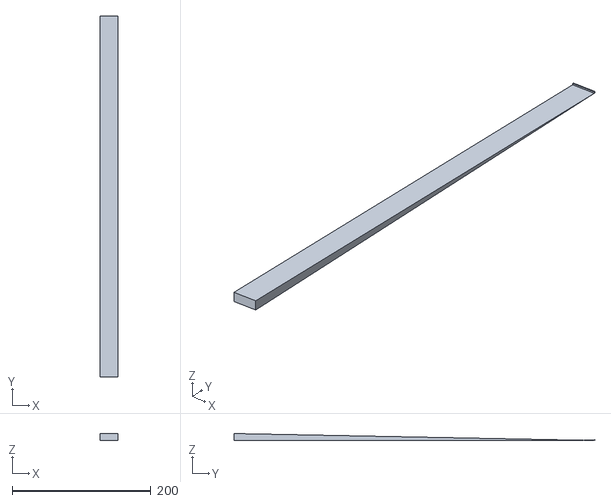
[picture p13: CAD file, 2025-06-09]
CAD/Halleffect_Sensor_Tuning/10degree_incline.stl
26.0 x 520.0 x 10.0

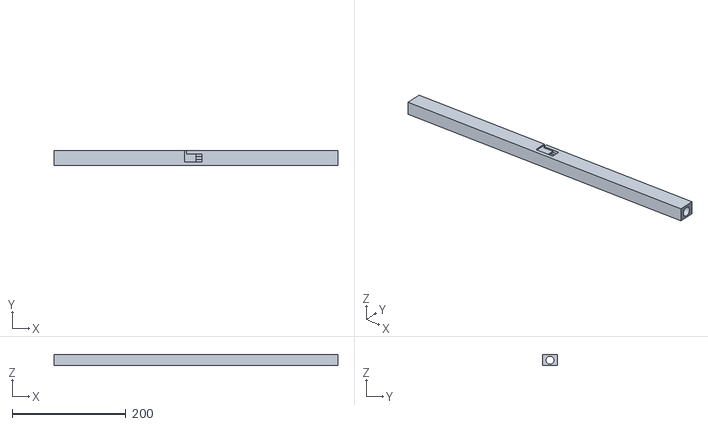
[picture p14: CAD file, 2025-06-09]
CAD/Halleffect_Sensor_Tuning/Hall_sensor.stl
500.0 x 26.0 x 20.0

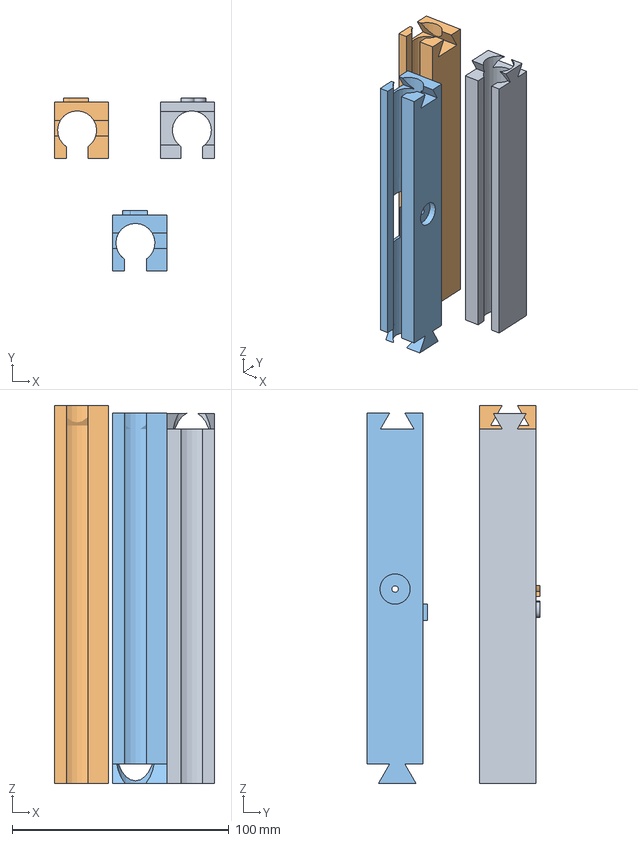
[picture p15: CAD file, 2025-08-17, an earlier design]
CAD/Halleffect_Sensor_Tuning/V2/Hall_sensor_testing.3mf
74.0 x 80.0 x 174.5 mm
Hall_sensor_testing_V4.stl_A_A
Hall_sensor_testing_V4.stl_B
Hall_sensor_testing_V4.stl_A_B

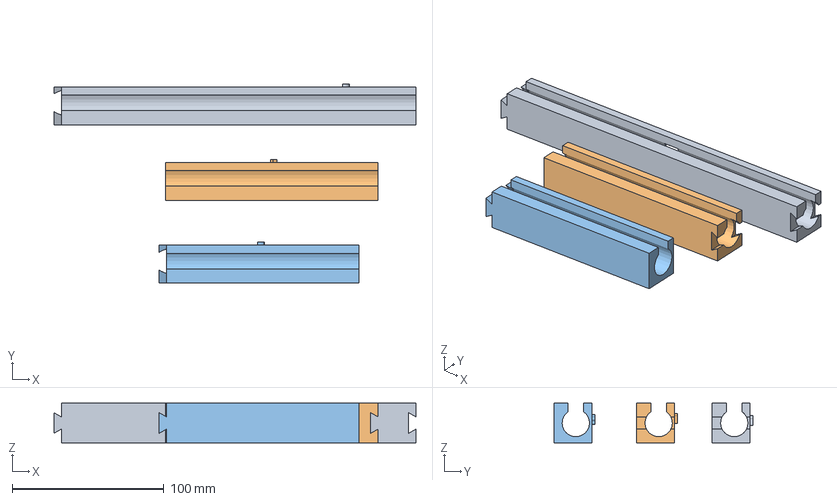
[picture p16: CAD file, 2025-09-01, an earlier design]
CAD/Halleffect_Sensor_Tuning/V3/Hall_effect_sensor_testing_V3 v3.3mf
238.3 x 131.3 x 26.0 mm
Hall_effect_sensor_testing_V3 v4.stl_B_A
Hall_effect_sensor_testing_V3 v4.stl_B_B
Hall_effect_sensor_testing_V3 v4.stl_A

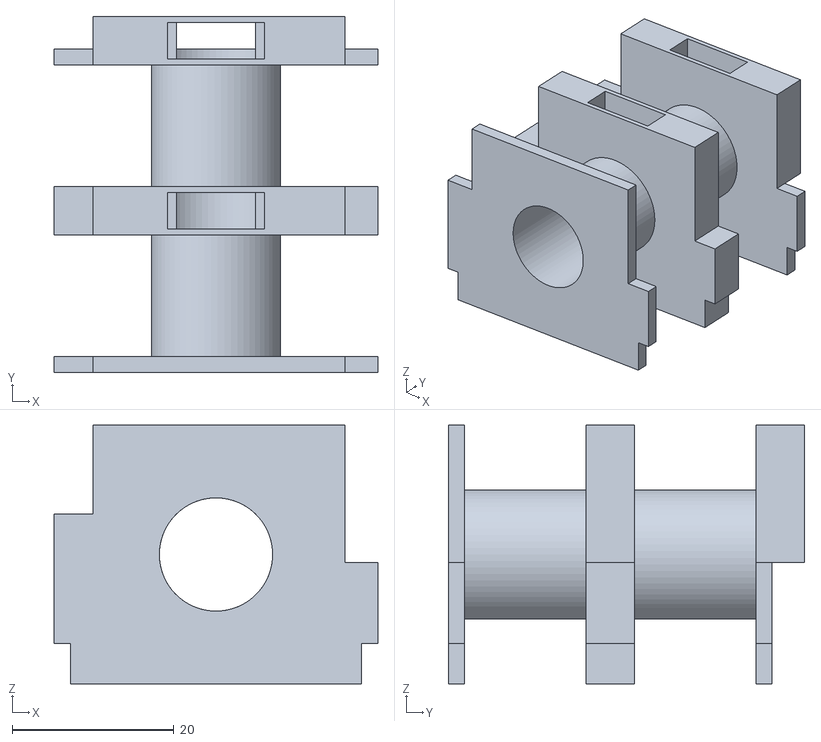
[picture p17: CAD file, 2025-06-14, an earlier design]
CAD/Coil_Redesign_Version1/Coil_Redesign_Part1.stl
40.0 x 44.0 x 32.0

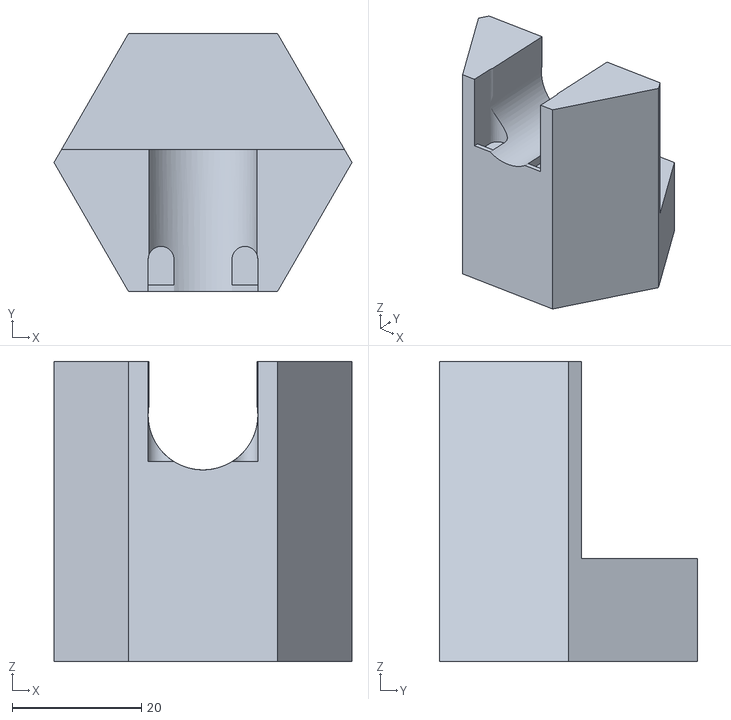
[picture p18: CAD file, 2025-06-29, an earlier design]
CAD/Coil_Redesign_Version2/Coil_redesign_Support_V2.stl
46.2 x 40.0 x 46.5

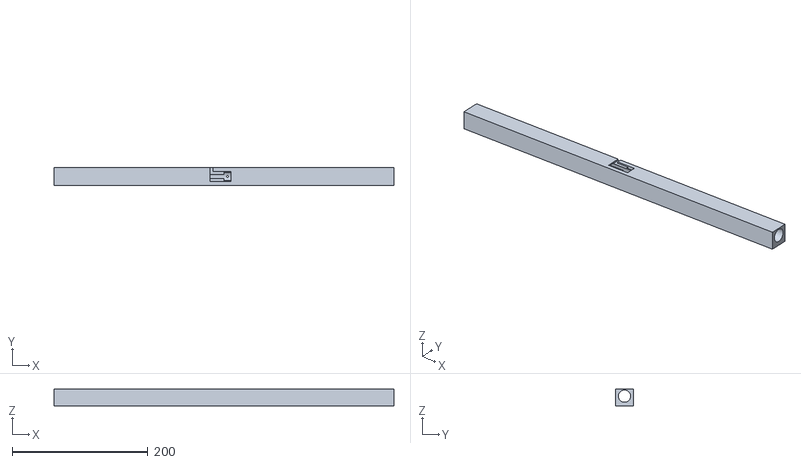
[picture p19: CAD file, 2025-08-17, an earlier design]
CAD/Halleffect_Sensor_Tuning/V2/Hall_effect_sensor_testing.stl
500.0 x 26.0 x 25.0

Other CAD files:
CAD/Coil_Redesign_Version1/base (redesign)-Body.stl
CAD/Coil_Redesign_Version2/Base_Body_V2.stl
CAD/Coil_Redesign_Version1/Coil_Redesign_Part2.3mf
CAD/Coil_Redesign_Version2/Coil_redesign_Tube_V2.stl
CAD/Coil_Redesign_Version1/Coil_Redesign_Part2.stl
CAD/Halleffect_Sensor_Tuning/V3/Hall_effect_sensor_testing_V3 v3.stl
CAD/Halleffect_Sensor_Tuning/V4/Hall_effect_sensor_testing_V3 v3.2.stl

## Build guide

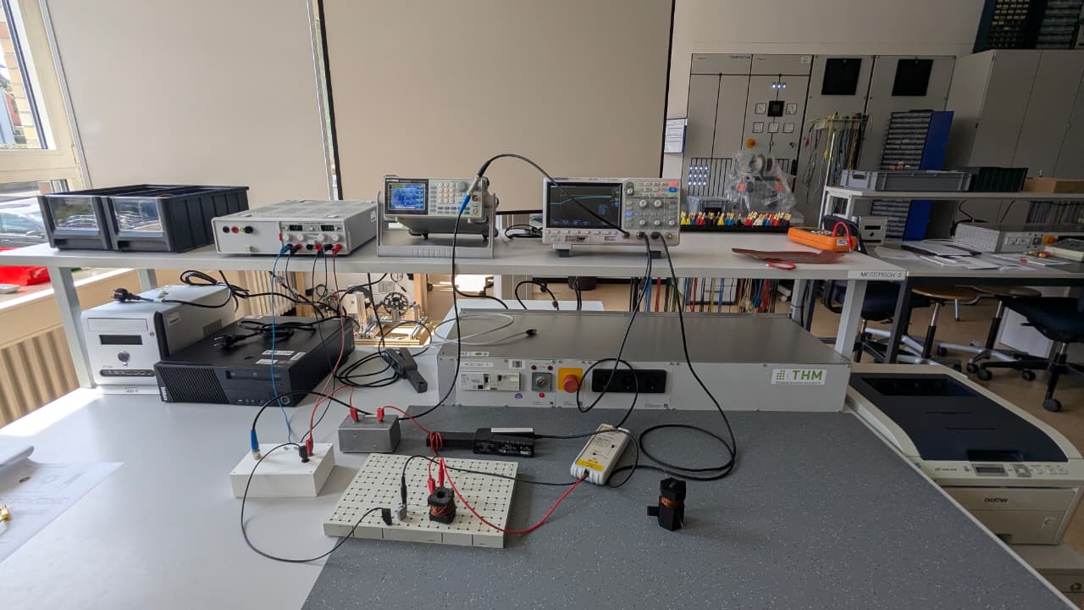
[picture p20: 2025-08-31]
Induction measurement/Experiment setup.jpeg

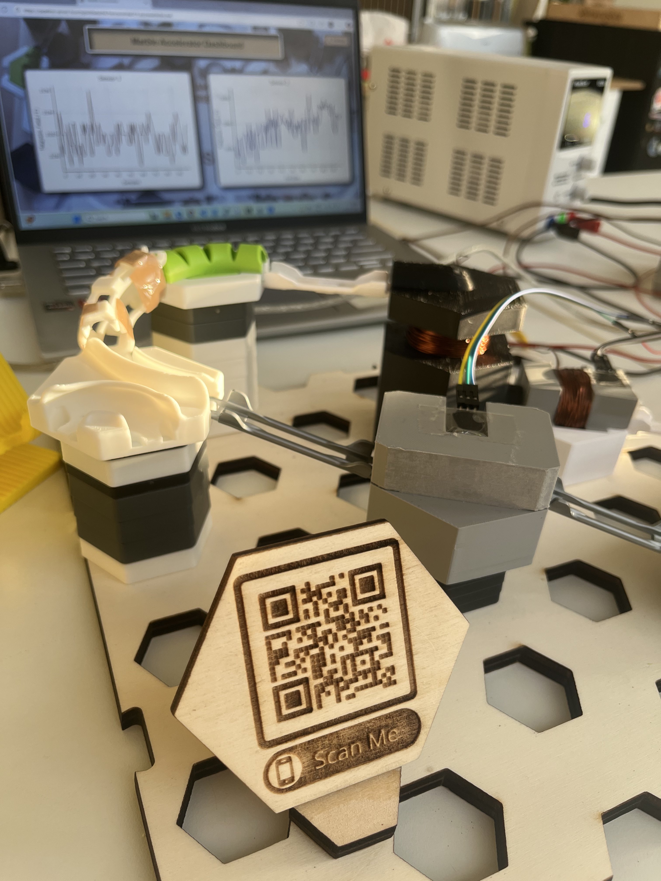
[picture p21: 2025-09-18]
Data_visualization/Fastapi_webserver/Result_img/QR_printed.jpg

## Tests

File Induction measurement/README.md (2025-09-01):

#Inductance Measurement Experiment 

The purpose of this experiment is to measure and analyze the inductance of electromagnet coils. By characterizing the inductance of different coil designs , we can optimize performance of coil.

#Equipment

In above Experiment setup file shows  equipments we used and connection we made for the experiment.

1). DC Power Supply
* It provides adjustable DC voltage and current for energizing the coil.

2). Function Generator (Signal Generator)
* It can produce different type of signals such as sinusoidal, square and triangular.
* Used to apply AC excitation signal to the coil for inductance measurement.

3). Oscilloscope 
* It captures and displays the time - domain waveform of voltage and current.
* We can observe phase difference between voltage and current.

4). Multimeter
* For direct measurement of coil´s resistance and inductance.

5). Breadboard
* We used custom breadboard where vertical group of 5 holes in the middle are connected internally.
* The long horizontal strips on the sides are power rails (positive and ground).

#About connection details of experiment

*The function generator is connected in series with coil and shunt resistor. Oscilloscope Channel 1 is connected across the coil and channel 2 is connected across the shunt resistor.
*Multimeter is directly connected across the coil to measure resistance.

#Experiment result on oscilloscope.

In Experiment result file we can see two different waveforms it indicates voltage and current characteristics.

*The yellow waveform is almost constant. It indicate the applied voltage from the function generator.
*The blue waveform shows a gradual rising curve, typical of current through an inductor. At the moment of voltage application, current starts at zero, then it increases gradually following an exponential curve,because coil stores energy in its magnetic field.
*The delay in current growth is direct effect of inductance.
*By measuring how fast the current rises (the time constant,T = L/R). the inductance of the coil can be calculated.

#Inductance result

* Here we got T(time constant) around 119μs on oscilloscope. Resistance value we got 5.8 Ω on multimeter.
* Inductance value is 689 μH.

#In project we are using two coils.Below are reistance and inductance values of both coil. 

1). Vertical Coil Resistance - 0.7126 Ω.
2). Vertical Coil Inductance - 686.6 μH. 
3). Horizontal Coil Resistance - 0.7644 Ω.
4). Horizontal Coil Inductance - 715.9 μH.

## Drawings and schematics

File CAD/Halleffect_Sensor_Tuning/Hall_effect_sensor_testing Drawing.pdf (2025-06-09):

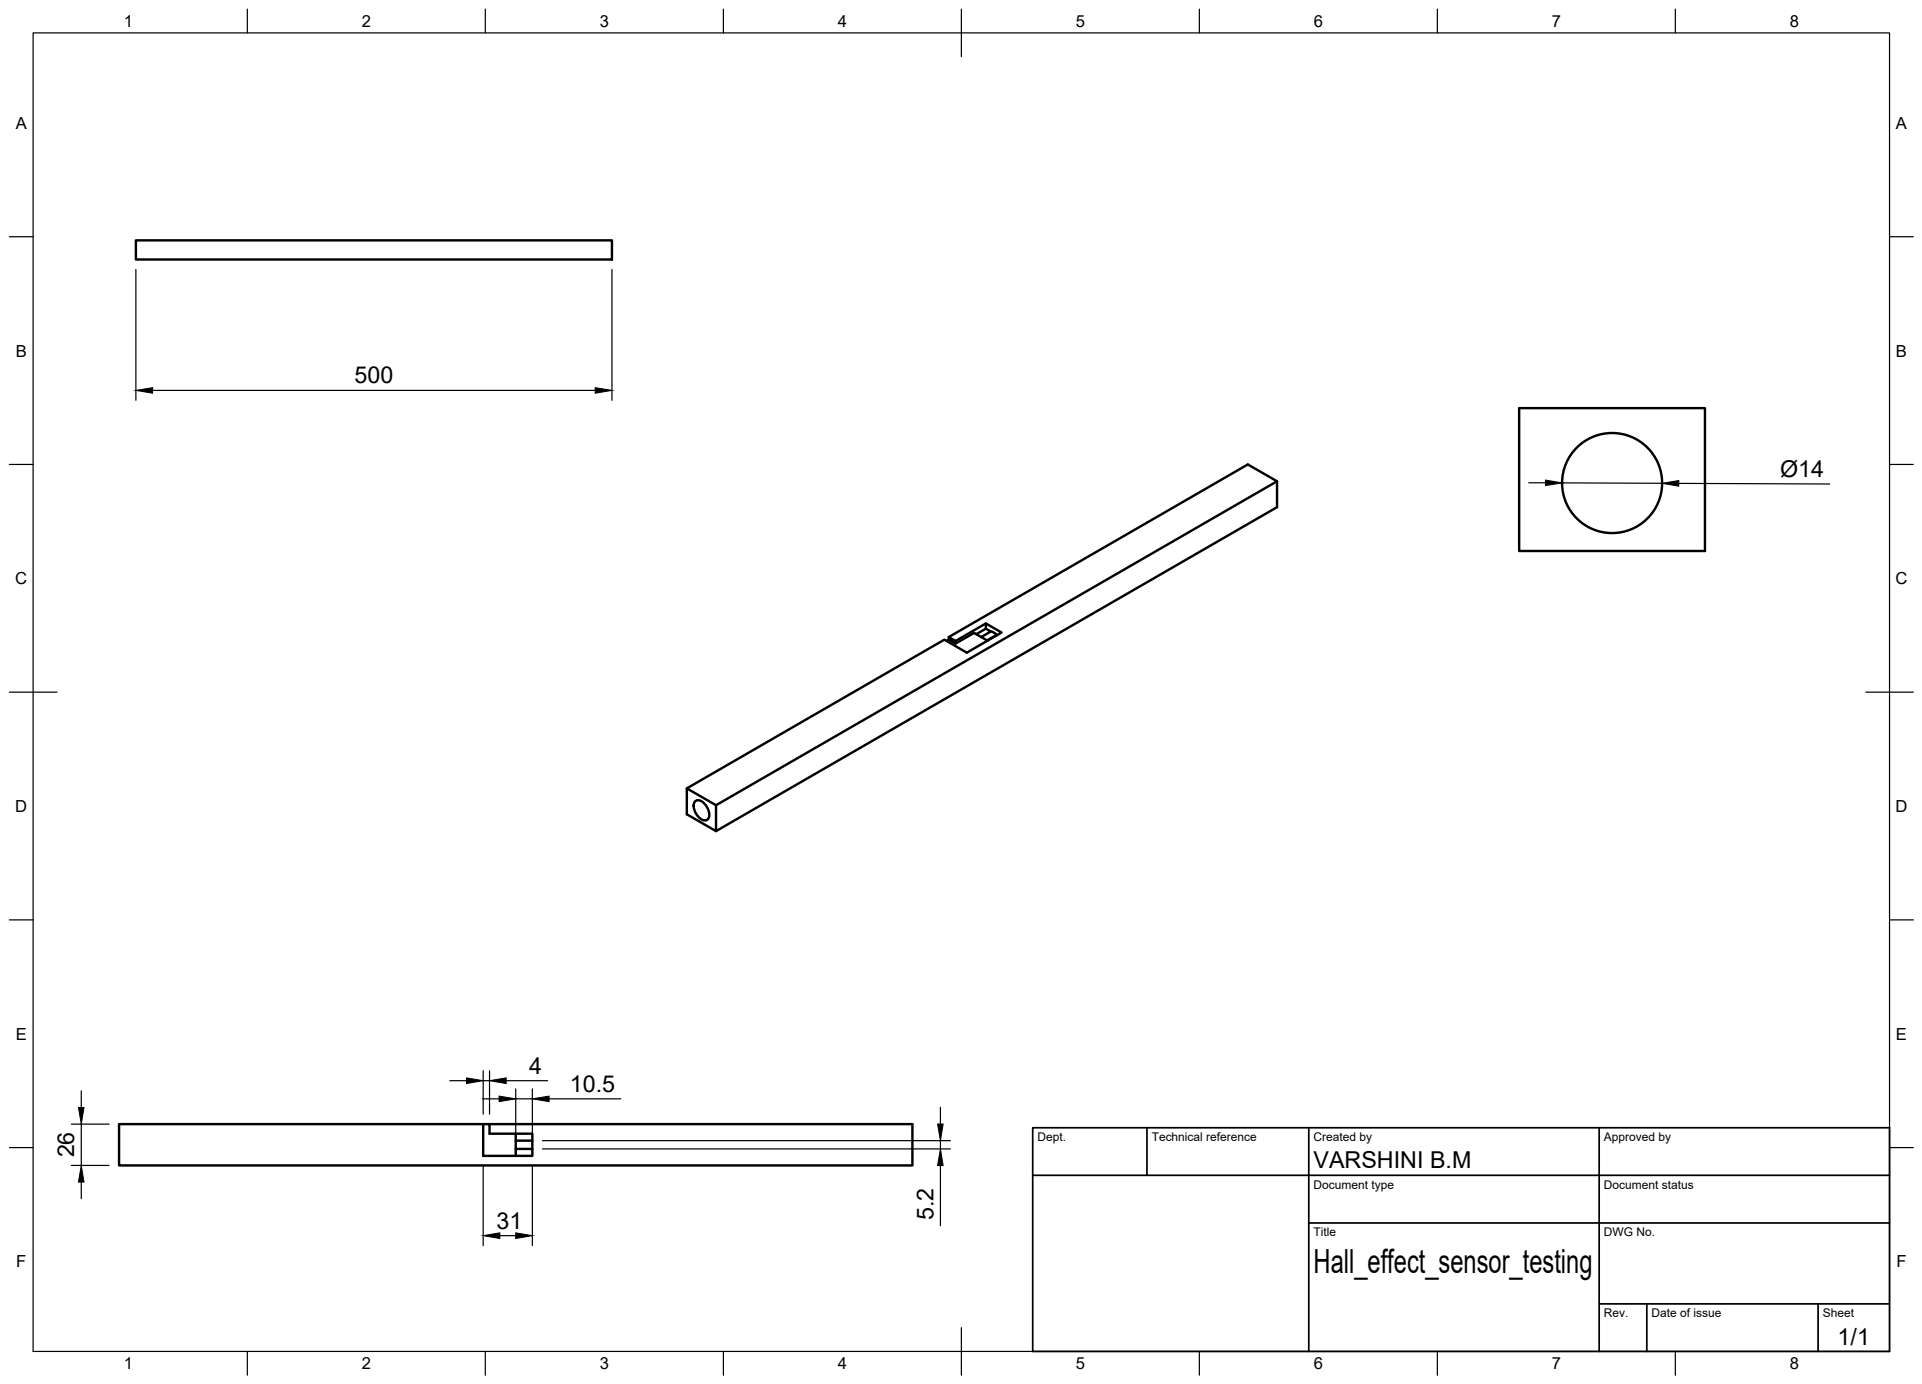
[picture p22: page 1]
Title; DWG No.; Rev.; Date of issue; Sheet

Dept. | Technical reference | Created by VARSHINI B.M | Approved by

Document type | Document status

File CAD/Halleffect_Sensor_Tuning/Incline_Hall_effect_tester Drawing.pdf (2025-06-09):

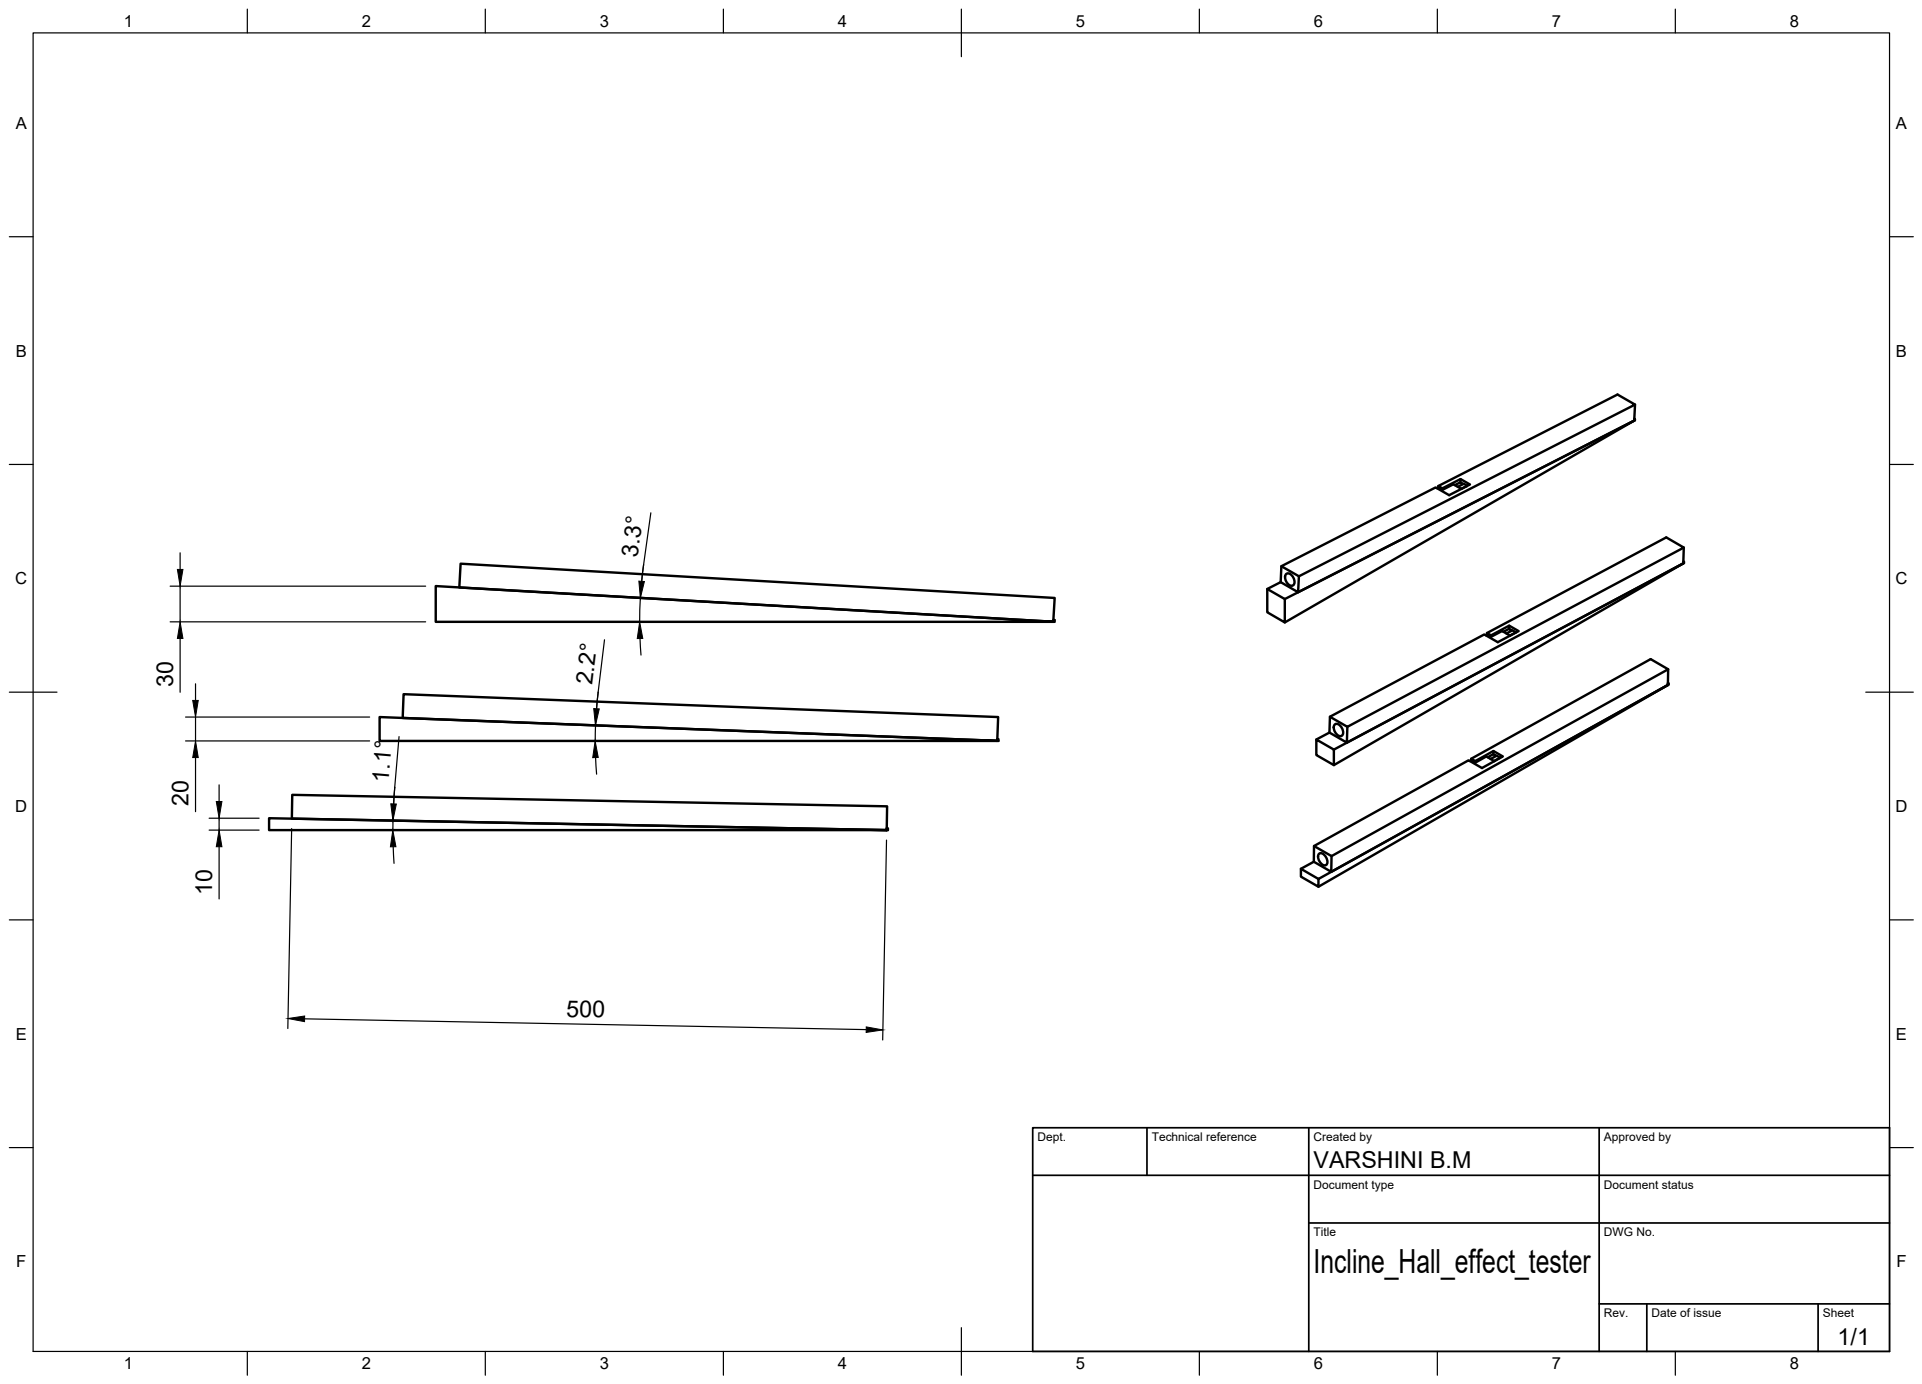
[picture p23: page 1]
Title; DWG No.; Rev.; Date of issue; Sheet; VARSHINI B.M 30 20 10

Dept. | Technical reference | Created by | Approved by

Document type | Document status

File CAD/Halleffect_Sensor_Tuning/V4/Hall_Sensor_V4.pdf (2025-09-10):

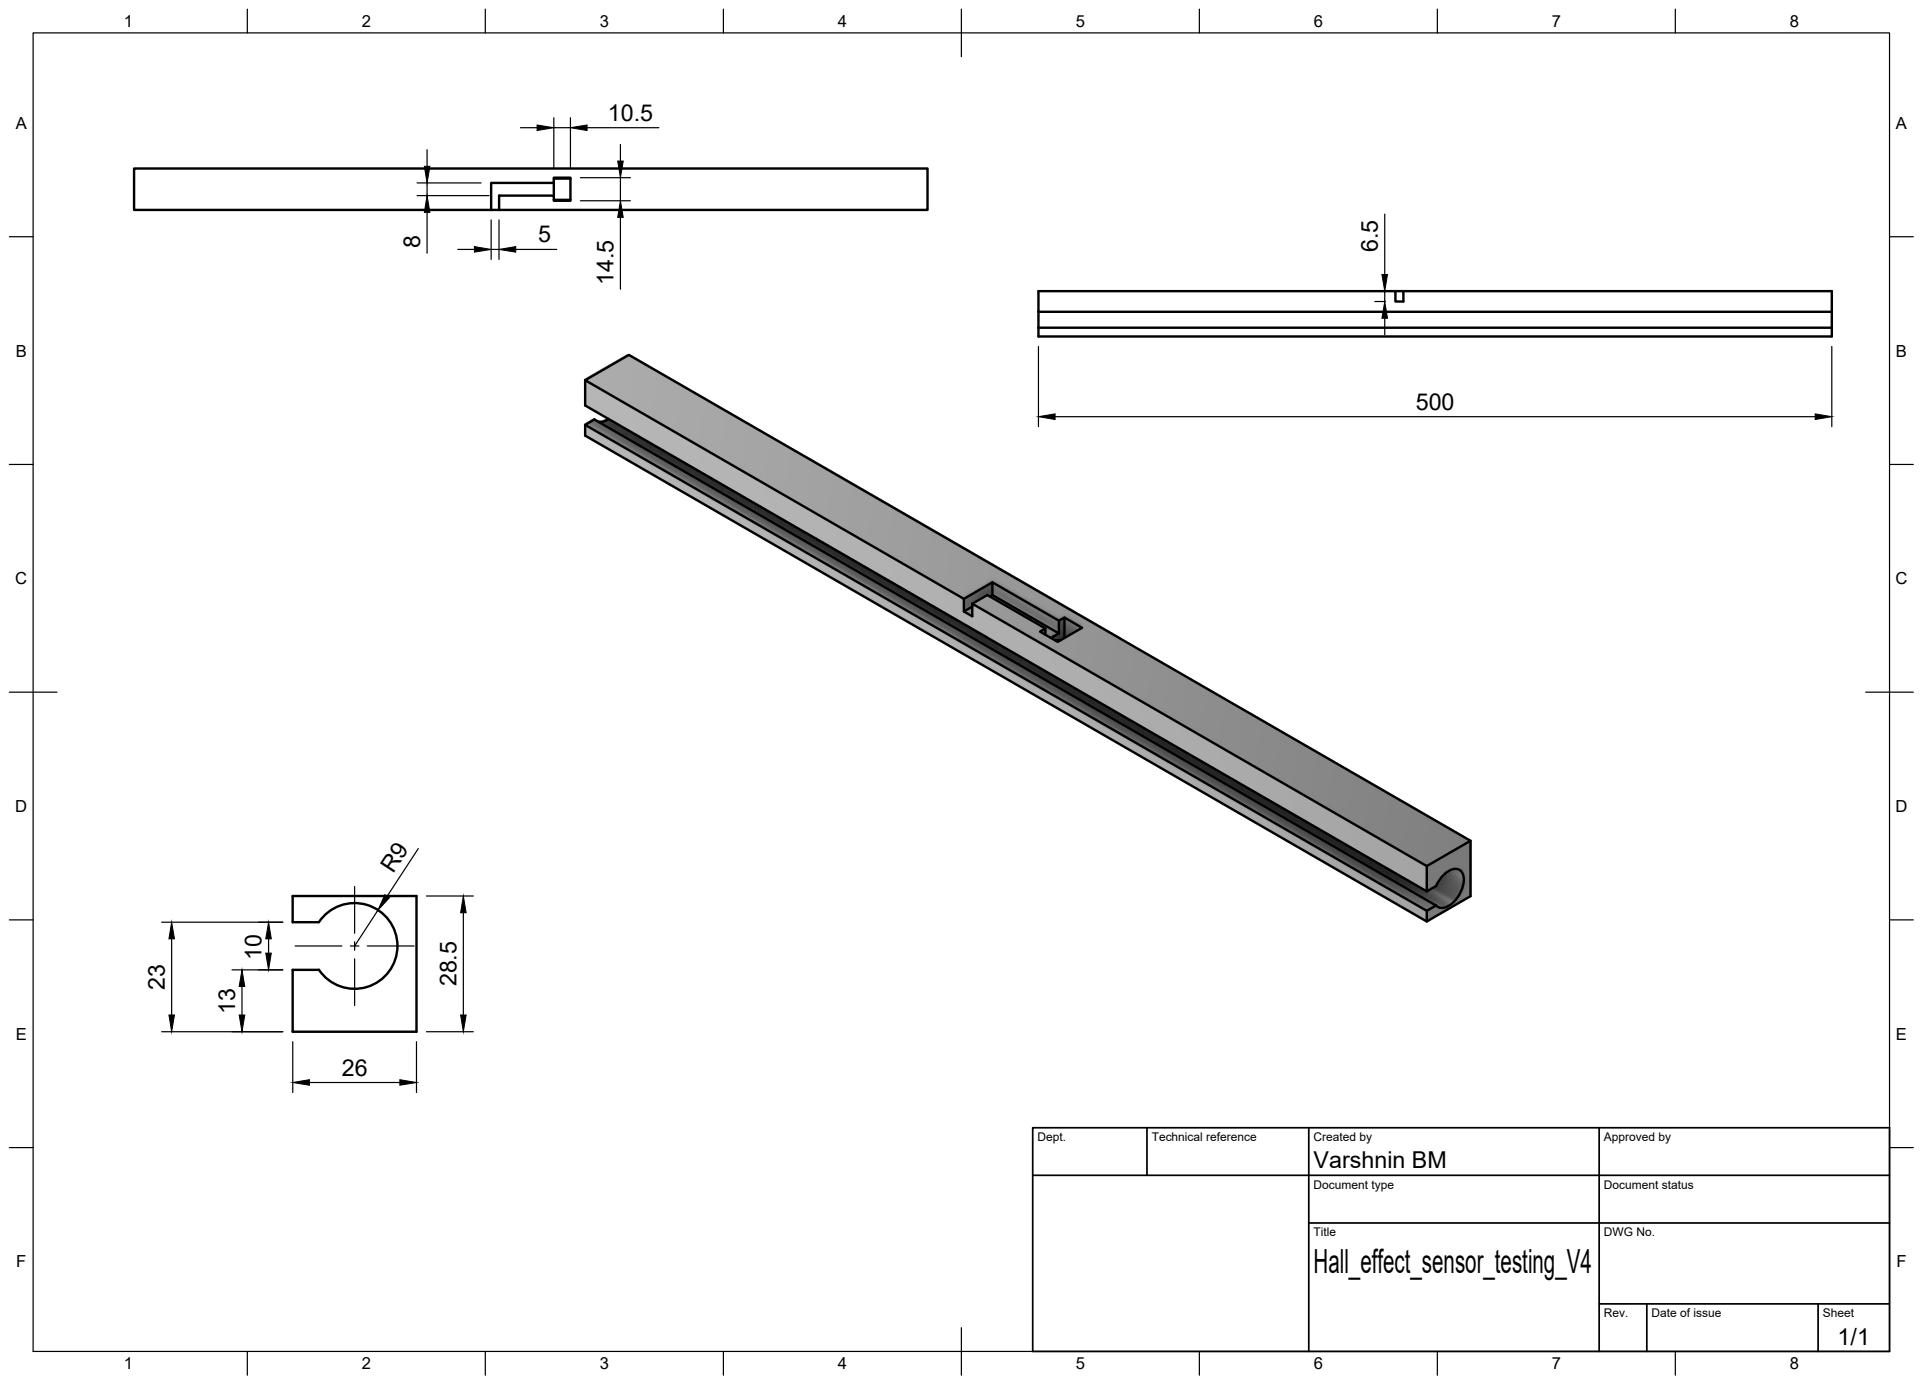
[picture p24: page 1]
Title; DWG No.; Rev.; Date of issue; Sheet

Dept. | Technical reference | Created by Varshnin BM | Approved by

Document type | Document status

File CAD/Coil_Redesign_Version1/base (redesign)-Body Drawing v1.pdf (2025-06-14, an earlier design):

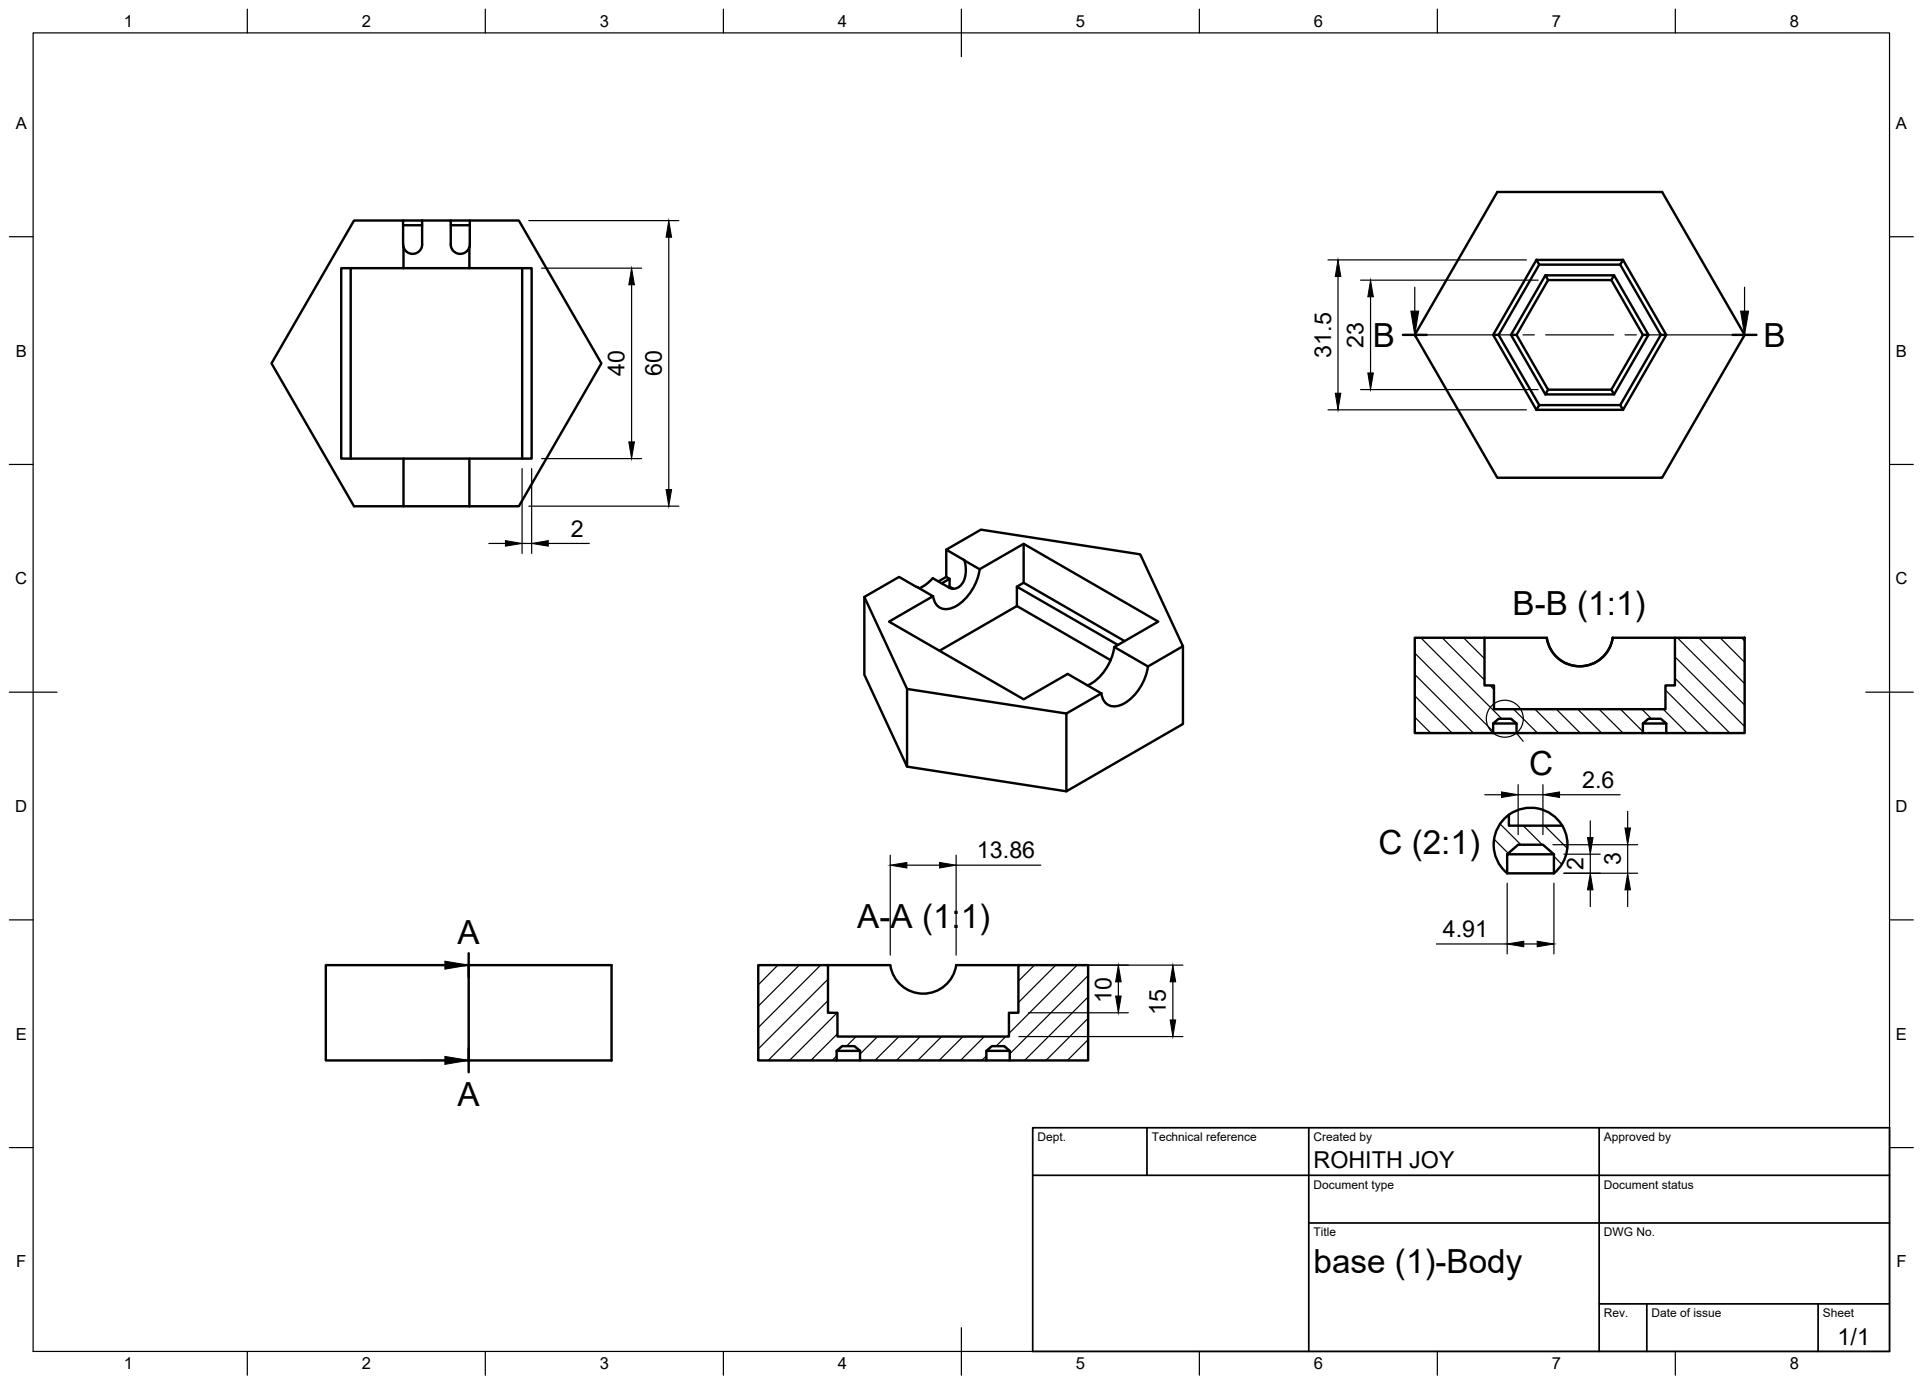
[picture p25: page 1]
Title; DWG No.; Rev.; Date of issue; Sheet; base (1)-Body; ROHITH JOY 40

Dept. | Technical reference | Created by | Approved by

Document type | Document status

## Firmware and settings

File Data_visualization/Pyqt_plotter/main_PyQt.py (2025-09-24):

import sys
import json
import serial
import time
import logging

from PyQt6 import QtCore, QtWidgets
from PyQt6.QtCharts import QChart, QChartView, QLineSeries, QValueAxis
from PyQt6.QtGui import QPainter, QFont
from PyQt6.QtCore import Qt

# =======================
# Serial configuration
# =======================
SERIAL_PORT = 'COM5'          # Update with your serial port (e.g., COMx on Windows, /dev/ttyUSBx on Linux)
BAUD_RATE = 115200            # Baud rate for serial communication
LOG_FILE = "serial_data_log.txt"  # File to save raw JSON (1 per line)

# =======================
# ADC conversion config
# =======================
V_REF = 3.3                  # Reference voltage of ADC (depends on hardware, e.g., 3.3V)
ADC_RESOLUTION = 12          # Bit resolution of ADC (e.g., 10-bit=1023, 12-bit=4095, etc.)

# =======================
# Debug and logger setup
# Debug level:
# 0 = no logs
# 1 = only errors
# 2 = warnings + info
# 3 = detailed debug logs
# =======================
debuglevel = 3

logging.basicConfig(
    level=logging.DEBUG,
    format="%(asctime)s [%(levelname)s] %(message)s",
    datefmt="%Y-%m-%d %H:%M:%S"
)
logger = logging.getLogger("PyQtSerialChart")


# =======================
# Helper: ADC → Voltage conversion
# =======================
def convert_to_voltage(raw_value):
    """
    Convert raw ADC value to voltage.
    raw_value: integer (0 ... 2^ADC_RESOLUTION-1)
    returns: float voltage in Volts
    """
    try:
        return raw_value * V_REF / (2**ADC_RESOLUTION - 1)
    except Exception:
        return None


# =======================
# Serial Reader Thread
# =======================
class SerialReader(QtCore.QThread):
    """
    Background thread for reading serial data.
    Continuously reads JSON lines from serial port and emits them via a Qt signal.
    """

    # Signal emitted when valid data is received (dict format)
    data_received = QtCore.pyqtSignal(dict)

    def __init__(self, port, baudrate):
        super().__init__()
        self.port = port
        self.baudrate = baudrate
        self.running = True
        try:
            self.ser = serial.Serial(self.port, self.baudrate, timeout=2)
            if debuglevel > 1:
                logger.info(f"Connected to {self.port}")
        except Exception as e:
            logger.error(f"Error opening serial port: {e}")
            self.ser = None

    def run(self):
        """Main loop: read serial data, parse JSON, and emit signal."""
        if not self.ser:
            return

        buffer = b""  # byte buffer
        while self.running:
            try:
                buffer += self.ser.read(self.ser.in_waiting or 1)

                while b"\n" in buffer:  # Split on newline (JSON per line)
                    line, buffer = buffer.split(b"\n", 1)
                    try:
                        line_str = line.decode("utf-8")
                    except UnicodeDecodeError:
                        continue

                    try:
                        # Parse JSON object
                        data = json.loads(line_str)

                        # Only process if it contains sensor keys
                        if any(k in data for k in ["D1", "D2"]):
                            if debuglevel > 2:
                                logger.debug("Valid JSON received, emitting signal")

                            # Save raw JSON (not converted) to log file
                            with open(LOG_FILE, "a") as f:
                                f.write(line_str.strip() + "\n")

                            # Emit data to UI
                            self.data_received.emit(data)
                            time.sleep(0.05)
                        else:
                            if debuglevel > 1:
                                logger.warning("JSON missing required keys")
                    except json.JSONDecodeError:
                        if debuglevel > 1:
                            logger.warning("Invalid JSON received: %s", line_str.strip())
                        continue
            except Exception as e:
                logger.error(f"Serial read error: {e}")
                break

    def stop(self):
        """Stop the thread and close serial port."""
        self.running = False
        if self.ser and self.ser.is_open:
            self.ser.close()
        self.wait()
        if debuglevel > 1:
            logger.info("SerialReader stopped")


# =======================
# Chart Widget
# =======================
class ChartWidget(QtWidgets.QWidget):
    """
    Main UI widget.
    Displays real-time charts for D1 and D2.
    """

    def __init__(self, serial_thread):
        super().__init__()
        self.serial_thread = serial_thread

        # Window setup
        self.setWindowTitle("PyQtChart Real-time Plot")
        main_layout = QtWidgets.QVBoxLayout(self)

        # Title label
        title_label = QtWidgets.QLabel("Marble Accelerator - Real Time Visualisation")
        title_label.setAlignment(Qt.AlignmentFlag.AlignCenter)
        title_label.setStyleSheet("font-size: 18px; font-weight: bold; padding: 5px;")
        main_layout.addWidget(title_label)

        # Grid layout to hold charts
        grid = QtWidgets.QGridLayout()
        main_layout.addLayout(grid)

        # Chart titles and axis labels
        self.titles = ["Sensor 1 (Voltage)", "Sensor 2 (Voltage)"]
        self.y_labels = ["Voltage (V)", "Voltage (V)"]
        self.x_labels = ["Samples", "Samples"]

        self.charts, self.series, self.y_axes = [], [], []

        # Create 2 charts (D1 and D2)
        for i, title in enumerate(self.titles):
            chart = QChart()
            chart.setTitle(title)
            chart.legend().hide()
            chart_view = QChartView(chart)
            chart_view.setRenderHint(QPainter.RenderHint.Antialiasing)

            # Line series (plot curve)
            s = QLineSeries()
            chart.addSeries(s)

            # X-axis setup
            axis_x = QValueAxis()
            axis_x.setRange(0, 100)  # default range, will auto-adjust
            axis_x.setTitleText(self.x_labels[i])
            axis_x.setTickCount(6)
            axis_x.setLabelFormat("%d")

            # Y-axis setup
            axis_y = QValueAxis()
            axis_y.setRange(0, V_REF)  # Voltage range (0 → V_REF)
            axis_y.setTitleText(self.y_labels[i])

            # Font size for labels
            font = QFont()
            font.setPointSize(7)
            axis_x.setLabelsFont(font)
            axis_y.setLabelsFont(font)

            # Attach axes
            chart.addAxis(axis_x, Qt.AlignmentFlag.AlignBottom)
            chart.addAxis(axis_y, Qt.AlignmentFlag.AlignLeft)
            s.attachAxis(axis_x)
            s.attachAxis(axis_y)

            # Place chart in grid (2x1 layout)
            row, col = i // 2, i % 2
            grid.addWidget(chart_view, row, col)

            self.charts.append(chart)
            self.series.append(s)
            self.y_axes.append(axis_y)

    @QtCore.pyqtSlot(dict)
    def update_data(self, data):
        """
        Update charts with new serial data.
        Converts raw ADC values → voltages before plotting.
        """
        d1 = data.get("D1")
        d2 = data.get("D2")

        data_list = [d1, d2]

        for i, y_data in enumerate(data_list):
            if y_data is None:
                self.series[i].clear()
                continue

            # Convert raw ADC values → Voltages
            converted = [convert_to_voltage(v) for v in y_data if v is not None]

            # X values = sample indices
            x = list(range(len(converted)))
            points = [QtCore.QPointF(xv, yv) for xv, yv in zip(x, converted)]
            self.series[i].replace(points)

            # Update X-axis dynamically
            axis_x = self.charts[i].axes(Qt.Orientation.Horizontal)[0]
            axis_x.setRange(0, len(x) - 1 if len(x) > 1 else 1)

            # Update Y-axis dynamically
            d_min, d_max = min(converted), max(converted)
            margin = (d_max - d_min) * 0.1 if abs(d_max - d_min) > 1e-6 else 0.1
            self.y_axes[i].setRange(max(0, d_min - margin), min(V_REF, d_max + margin))

        if debuglevel > 2:
            logger.debug("Charts updated with new converted data")


# =======================
# Application Entry Point
# =======================
def main():
    """Initialize application, start serial reader, and launch GUI."""
    app_qt = QtWidgets.QApplication(sys.argv)

    # Start background serial thread
    serial_thread = SerialReader(SERIAL_PORT, BAUD_RATE)

    # Create chart widget
    w = ChartWidget(serial_thread)
    w.resize(800, 600)
    w.show()

    logger.info("Visualization started — charts are ready and listening for data.")
    serial_thread.data_received.connect(w.update_data)
    serial_thread.start()

    # Ensure serial thread stops when app exits
    def on_exit():
        serial_thread.stop()
        if debuglevel > 1:
            logger.info("Application exiting, serial thread stopped")

    app_qt.aboutToQuit.connect(on_exit)
    logger.info("Application running — press Ctrl+C or close window to exit.")
    sys.exit(app_qt.exec())


if __name__ == "__main__":
    main()

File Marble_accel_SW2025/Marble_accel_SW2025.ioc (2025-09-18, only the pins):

Mcu.UserName=STM32L476RGTx
PA0.Signal=ADCx_IN5
PA1.Signal=ADCx_IN6
PA10.Signal=S_TIM1_CH3
PA2.GPIO_Label=USART_TX
PA2.Signal=USART2_TX
PA3.GPIO_Label=USART_RX
PA3.Signal=USART2_RX
PA5.GPIO_Label=LD2 [green Led]
PA5.Signal=GPIO_Output
PB10.Signal=S_TIM2_CH3
PC13.GPIO_Label=B1 [Blue PushButton]
PC13.Signal=GPXTI13
PC4.GPIO_Label=LED_BLINK
PC4.Signal=GPIO_Output

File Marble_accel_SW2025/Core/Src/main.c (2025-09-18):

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
/* Includes ------------------------------------------------------------------*/
#include "main.h"
#include "adc.h"
#include "tim.h"
#include "usart.h"
#include "gpio.h"

/* USER CODE BEGIN Includes */
#include "stdio.h"
/* USER CODE END Includes */

/* USER CODE BEGIN PD */
/**
  * @brief  Enable the TIM peripheral.
  * @param  __HANDLE__ TIM handle
  * @retval None
  */

//#define HAL_TIM_ENABLE_OPM(__HANDLE__)                 ((__HANDLE__)->Instance->CR1|=(TIM_CR1_CEN|TIM_CR1_OPM))
/* USER CODE END PD */


/* USER CODE BEGIN PV */
uint32_t mag_hor = 0;
uint32_t mag_ver = 0;
//uint32_t count=0;
//extern uint32_t marble_inside_flag;
//extern uint32_t marble_exit_flag;
//extern uint32_t marble_count;
extern uint32_t adc1_new_val_flag;
extern uint32_t adc2_new_val_flag;

extern bool is_buffone_full;
extern bool is_bufftwo_full;

uint32_t pv_count=0;

/* USER CODE END PV */

void SystemClock_Config(void);
void PeriphCommonClock_Config(void);
/**
  * @brief  The application entry point.
  * @retval int
  */
int main(void)
{

  /* MCU Configuration--------------------------------------------------------*/

  /* Reset of all peripherals, Initializes the Flash interface and the Systick. */
  HAL_Init();

  /* Configure the system clock */
  SystemClock_Config();

  /* Configure the peripherals common clocks */
  PeriphCommonClock_Config();

  /* Initialize all configured peripherals */
  MX_GPIO_Init();
  MX_USART2_UART_Init();
  MX_ADC1_Init();
  MX_TIM3_Init();
  MX_TIM1_Init();
  MX_ADC2_Init();
  MX_TIM2_Init();
  /* USER CODE BEGIN 2 */
  HAL_ADCEx_Calibration_Start(&hadc1,ADC_SINGLE_ENDED);
  HAL_ADCEx_Calibration_Start(&hadc2,ADC_SINGLE_ENDED);
  HAL_ADC_Start_IT(&hadc1);
  HAL_ADC_Start_IT(&hadc2);
  HAL_TIM_Base_Start_IT(&htim3);


  /* USER CODE END 2 */

  /* Infinite loop */
  /* USER CODE BEGIN WHILE */
  while (1)
  {
	  if (is_buffone_full || is_bufftwo_full)
	  {
		  send_data_json_array();
	  }
	  HAL_Delay(1);
    /* USER CODE END WHILE */

    /* USER CODE BEGIN 3 */
  }
  /* USER CODE END 3 */
}

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


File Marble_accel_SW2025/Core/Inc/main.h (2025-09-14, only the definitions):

#define tim2_period 10000-1
#define tim1_period 10000-1
#define tim2_duty 5000-1
#define tim1_duty 5000-1
#define B1_Pin GPIO_PIN_13
#define B1_GPIO_Port GPIOC
#define USART_TX_Pin GPIO_PIN_2
#define USART_TX_GPIO_Port GPIOA
#define USART_RX_Pin GPIO_PIN_3
#define USART_RX_GPIO_Port GPIOA
#define LD2_Pin GPIO_PIN_5
#define LD2_GPIO_Port GPIOA
#define LED_BLINK_Pin GPIO_PIN_4
#define LED_BLINK_GPIO_Port GPIOC
#define TMS_Pin GPIO_PIN_13
#define TMS_GPIO_Port GPIOA
#define TCK_Pin GPIO_PIN_14
#define TCK_GPIO_Port GPIOA
#define SWO_Pin GPIO_PIN_3
#define SWO_GPIO_Port GPIOB

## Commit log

2025-05-08 file moved to subfolder
    [base Drawing.FCStd]
2025-05-28 Create feature_plots.py
    plots created on sample data
2025-05-30 Add files via upload
    Plotting of the values from sample data
2025-06-01 Added systick config, 1 ms systick count tim3 enabled for 10khz up counter with interrupt. Defined json format for sending data.
2025-06-12 Capacitors added
2025-06-24 added the file
    [Coil Wire Calculation.csv]
2025-07-02 power supply
2025-08-12 Add files via upload
    updated chart structure, power button added
2025-08-26 Add files via upload
    Result pic of Demo data from STM32
2025-09-04 Removed All warning and errors. Not tested on board. Will add patch if not found working on STM32 Board. Need to do documentation.
    [CCCE_Demo_Code.ioc, main.c]
2025-09-04 coil holder redesign accoring to hall sensor
2025-09-09 SerialReader class now working correctly: start method implemented
    [plot_graphs_webserver.py]
2025-09-12 Create Coil wire calculation
2025-09-13 Initial Marble software commit. Separate peripheral files. Each peripheral file includes code for its tasks. Lots of testing code present but commented. Will be removed after one successful run.
    Not happy with TIM3 code, needs to be implemented in a better way or moved to adc peripheral. Moving to adc peripheral would be nice if a IIR filter is implemented on it. As it stands it is initial offset based.
    Main control of the code is from TIM3 interrupt. Dosent interfere with UART sending.
    Data being sent is just two values that are
    Mag_ver_sensor
    Mag_hor_sensor
    Task remaining:
    7 warnings
    Clean up commented code!!!!!!
    Check adc division!!!!!!!!
    uart receiving needs to be added.
    HAL_DELAY(1) N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
    [Marble_accel_SW2025.ioc, adc.c, main.c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]
2025-09-14 Added Uart receive support for testing.
2025-09-14 added new directory and files
    [Clean_force_table.csv]
2025-09-16 old sample data
2025-09-16 old sample_plots_JSON.png
2025-09-16 web initial setup sample
2025-09-16 Ngrok tunnelling and qrcode scanning :security issue :solved in azure deployment
    [main.py]
2025-09-16 old sample o/p
2025-09-17 Added Download button, changed GUI,alignment fix
2025-09-18 result images -sensor magnetic field
2025-09-18 QR printed - azure api
2025-09-18 Realtime data from stm32
2025-09-18 realtime sensor json data

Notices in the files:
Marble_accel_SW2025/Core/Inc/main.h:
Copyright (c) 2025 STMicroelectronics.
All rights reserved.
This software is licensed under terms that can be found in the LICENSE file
